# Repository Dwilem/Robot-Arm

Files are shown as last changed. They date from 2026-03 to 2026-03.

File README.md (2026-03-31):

# Robot-Arm
# Description
Pretty basic robotic 5 axis robotic arm, containing these axis: base, shoulder, elboew, wristx, wristy. To recreate this project, you can 3d print it, assemble it and upload provided firmware.

# Why
My main goal building such device, was deepen my knowledge of robotics, improve my electrical and mechanical fields. As well it is pretty cool project in general.

# Notes 
- Altough my main idea was to add camera to it, it turned out to be way more complicated, so I dumped that idea.
- If you want smoother movement of arm, I don't recommend buying cheapest knock-off motors and instead investing a bit more money into this. As I described in my journal, motors I bought were falsly advertised, so robot was failing :/.
- I recommend using different power supplys for Esp and motors, due to stability issues.
- Blue parts in Model\Asembly.step showcase where perf boards and esp is mounted.
- Perf boards serve as place for pin heads to be soldered on, so entire assmebly would be easier to take appart and maintain, without constant resoldering.

# Gallery
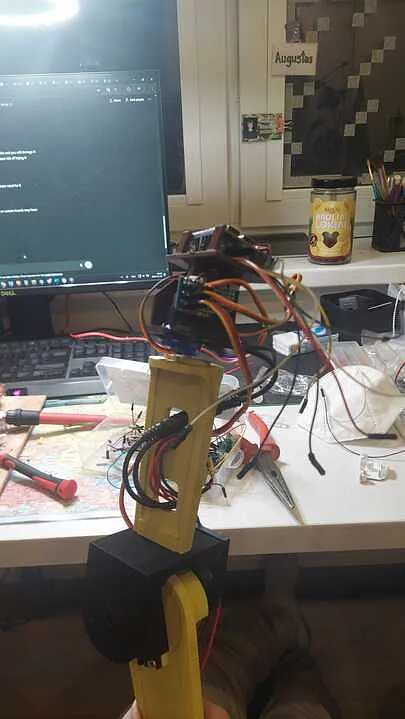
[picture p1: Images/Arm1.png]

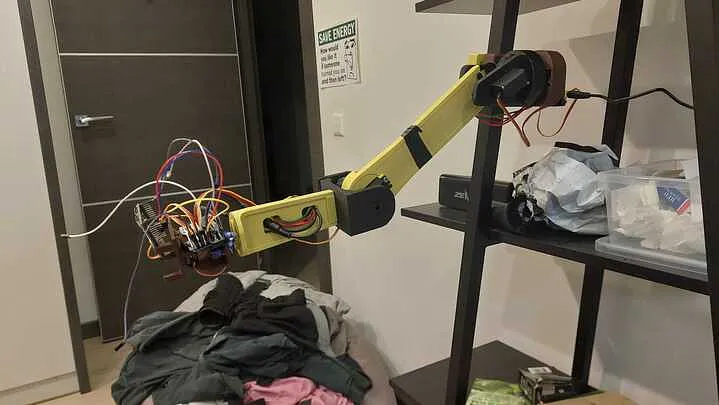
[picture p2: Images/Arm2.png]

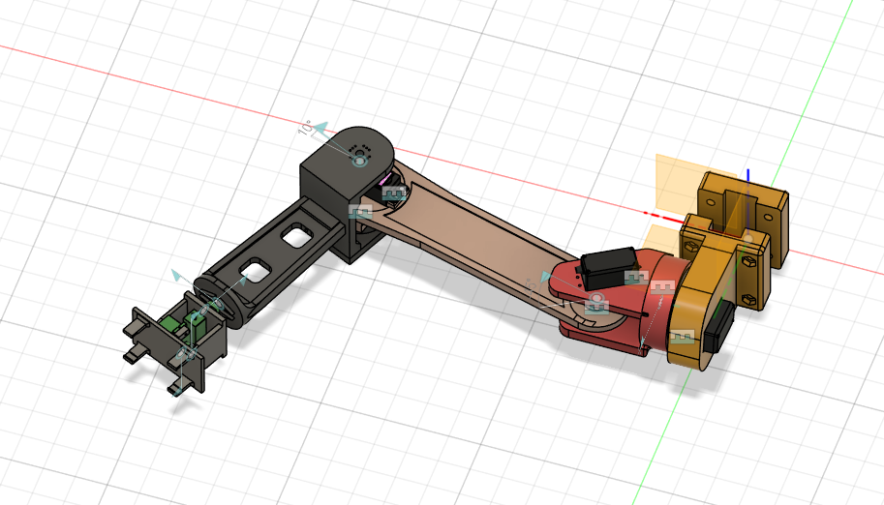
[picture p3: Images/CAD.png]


# Wiring
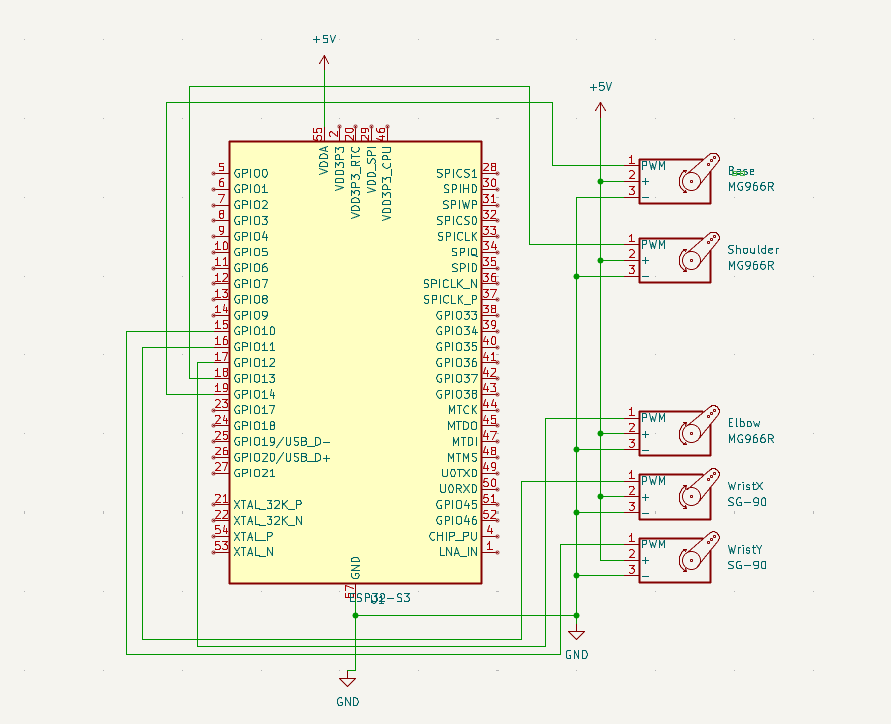
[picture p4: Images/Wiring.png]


# BOM
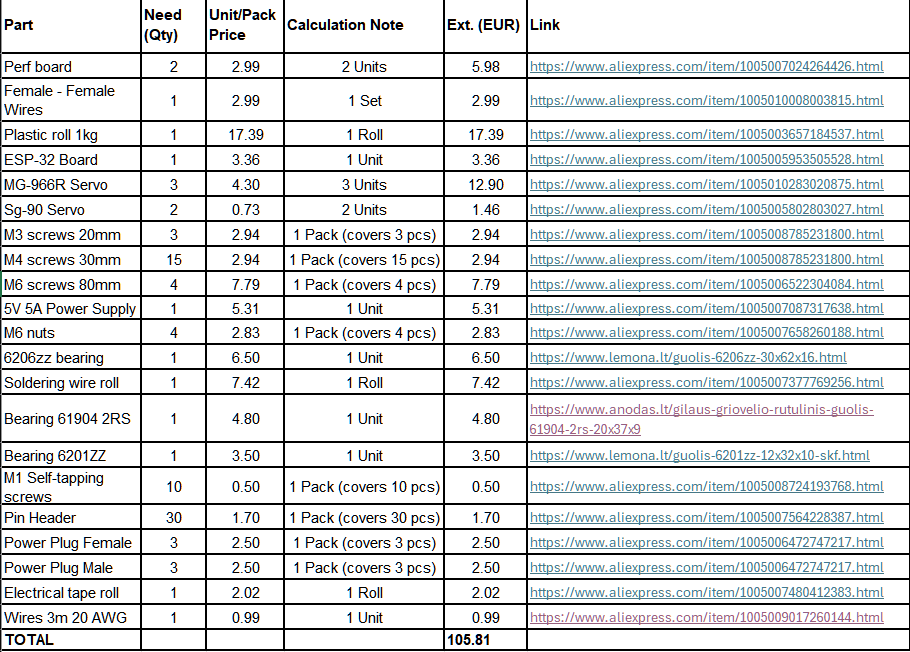
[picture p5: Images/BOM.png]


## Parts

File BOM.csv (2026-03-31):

Part | Need (Qty) | Unit/Pack Price | Calculation Note | Ext. (EUR) | Link
Perf board | 2 | 2.99 | 2 Units | 5.98 | https://www.aliexpress.com/item/1005007024264426.html
Female - Female Wires | 1 | 2.99 | 1 Set | 2.99 | https://www.aliexpress.com/item/1005010008003815.html
Plastic roll 1kg | 1 | 17.39 | 1 Roll | 17.39 | https://www.aliexpress.com/item/1005003657184537.html
ESP-32 Board | 1 | 3.36 | 1 Unit | 3.36 | https://www.aliexpress.com/item/1005005953505528.html
MG-966R Servo | 3 | 4.30 | 3 Units | 12.90 | https://www.aliexpress.com/item/1005010283020875.html
Sg-90 Servo | 2 | 0.73 | 2 Units | 1.46 | https://www.aliexpress.com/item/1005005802803027.html
M3 screws 20mm | 3 | 2.94 | 1 Pack (covers 3 pcs) | 2.94 | https://www.aliexpress.com/item/1005008785231800.html
M4 screws 30mm | 15 | 2.94 | 1 Pack (covers 15 pcs) | 2.94 | https://www.aliexpress.com/item/1005008785231800.html
M6 screws 80mm | 4 | 7.79 | 1 Pack (covers 4 pcs) | 7.79 | https://www.aliexpress.com/item/1005006522304084.html
5V 5A Power Supply | 1 | 5.31 | 1 Unit | 5.31 | https://www.aliexpress.com/item/1005007087317638.html
M6 nuts | 4 | 2.83 | 1 Pack (covers 4 pcs) | 2.83 | https://www.aliexpress.com/item/1005007658260188.html
6206zz bearing | 1 | 6.50 | 1 Unit | 6.50 | https://www.lemona.lt/guolis-6206zz-30x62x16.html
Soldering wire roll | 1 | 7.42 | 1 Roll | 7.42 | https://www.aliexpress.com/item/1005007377769256.html
Bearing 61904 2RS | 1 | 4.80 | 1 Unit | 4.80 | https://www.anodas.lt/gilaus-griovelio-rutulinis-guolis-61904-2rs-20x37x9
Bearing 6201ZZ | 1 | 3.50 | 1 Unit | 3.50 | https://www.lemona.lt/guolis-6201zz-12x32x10-skf.html
M1 Self-tapping screws | 10 | 0.50 | 1 Pack (covers 10 pcs) | 0.50 | https://www.aliexpress.com/item/1005008724193768.html
Pin Header | 30 | 1.70 | 1 Pack (covers 30 pcs) | 1.70 | https://www.aliexpress.com/item/1005007564228387.html
Power Plug Female | 3 | 2.50 | 1 Pack (covers 3 pcs) | 2.50 | https://www.aliexpress.com/item/1005006472747217.html
Power Plug Male | 3 | 2.50 | 1 Pack (covers 3 pcs) | 2.50 | https://www.aliexpress.com/item/1005006472747217.html
Electrical tape roll | 1 | 2.02 | 1 Roll | 2.02 | https://www.aliexpress.com/item/1005007480412383.html
Wires 3m 20 AWG | 1 | 0.99 | 1 Unit | 0.99 | https://www.aliexpress.com/item/1005009017260144.html
TOTAL |  |  |  | 105.81

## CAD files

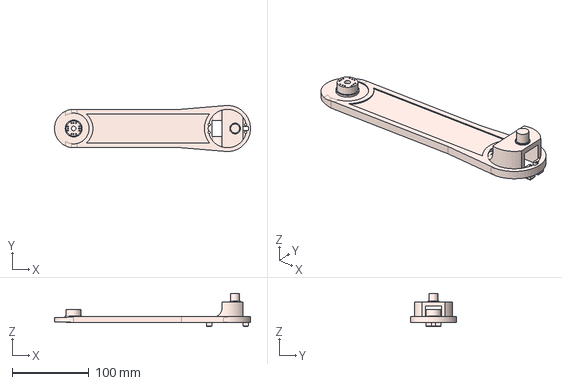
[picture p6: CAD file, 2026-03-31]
Model/Arm1/Arm1.step
255.0 x 60.0 x 43.0 mm

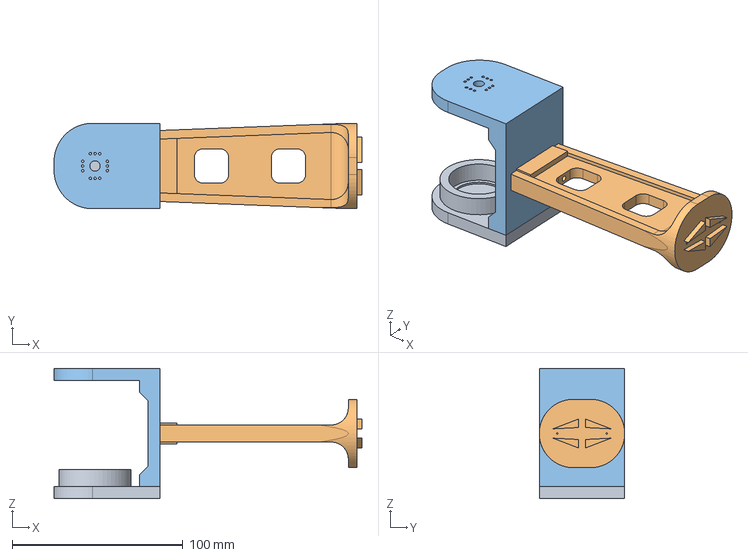
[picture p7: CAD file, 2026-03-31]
Model/Arm2/Arm2.step
180.1 x 50.0 x 76.2 mm

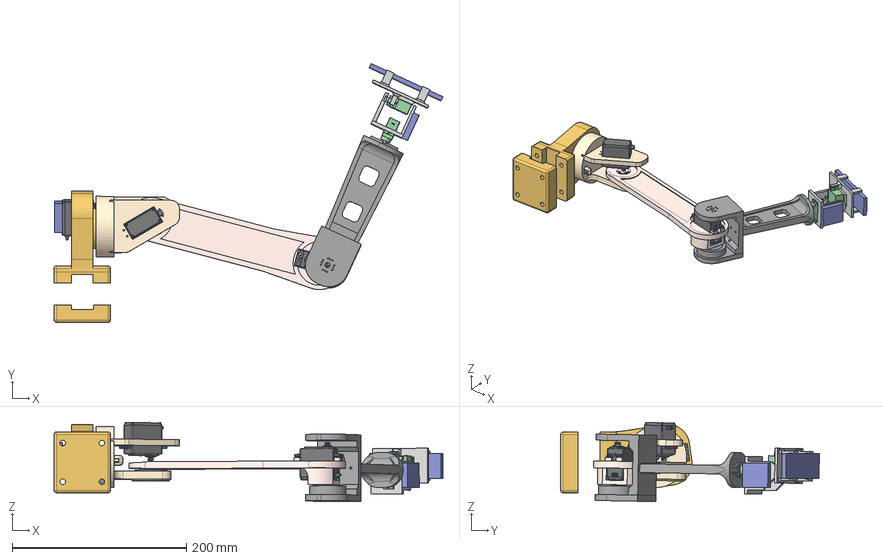
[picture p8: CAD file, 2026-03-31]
Model/Asembly.step
446.4 x 297.0 x 90.9 mm
Servo+MG996R x 3
Base
guolis-6206zz-30x62x16
Shoulder
Arm
servo x 2
splined-drive x 2
Wrist
Wrist2
Guolis 37-20-9
Guolis 32-20-10

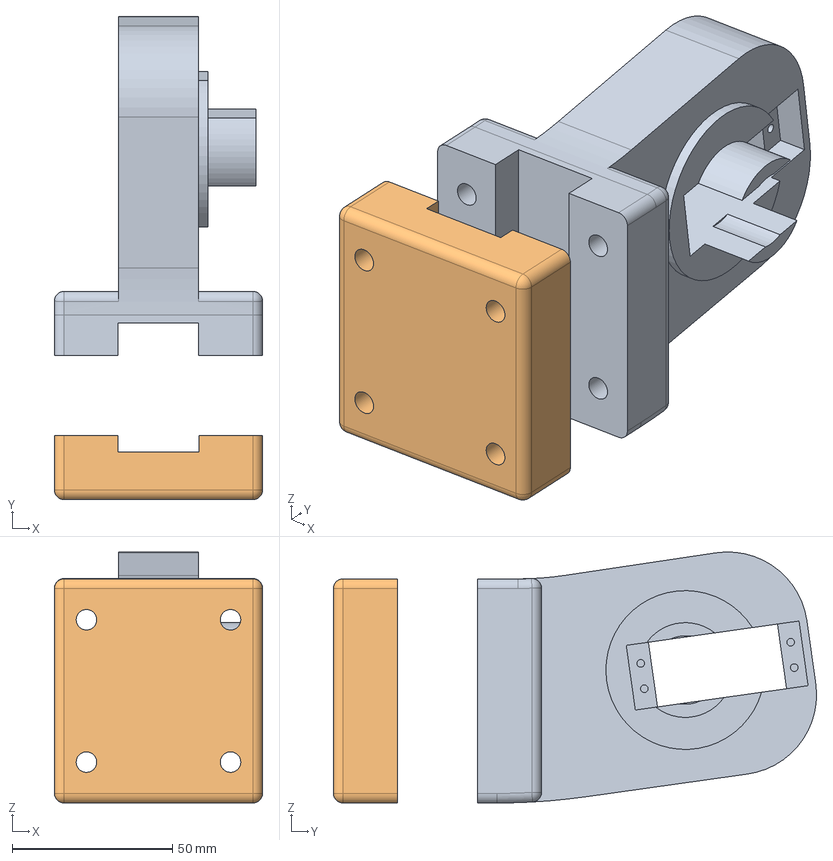
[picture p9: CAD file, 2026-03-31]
Model/Base/Base.step
65.0 x 150.9 x 78.4 mm

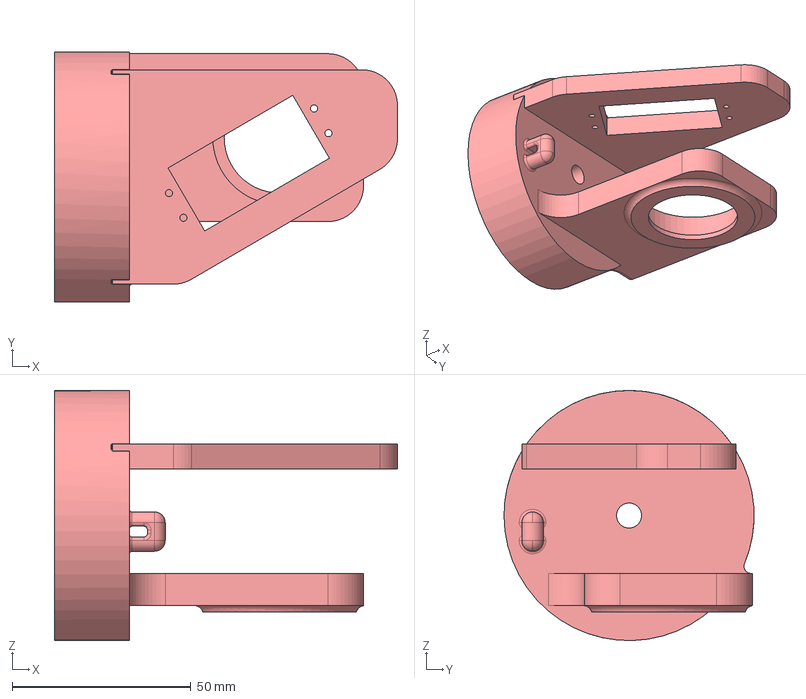
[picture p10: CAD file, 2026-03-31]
Model/Shoulder/Shoulder.step
96.0 x 70.0 x 70.0 mm

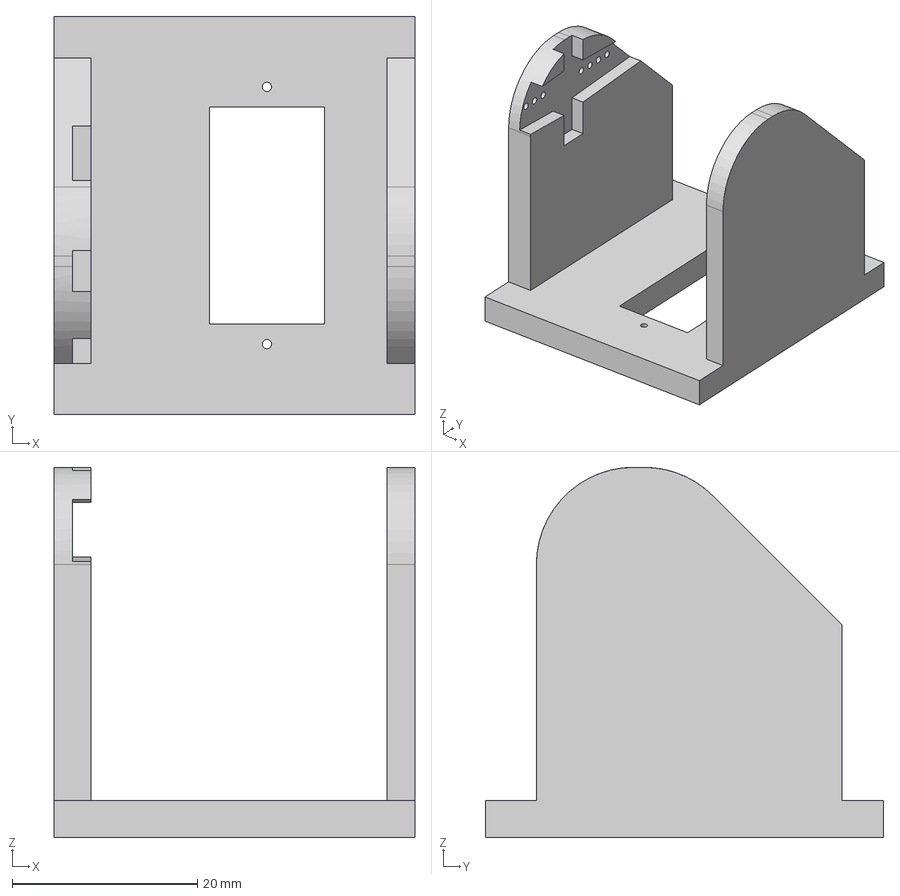
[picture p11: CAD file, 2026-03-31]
Model/Wrist1/Wrist1.step
39.0 x 43.0 x 40.0 mm

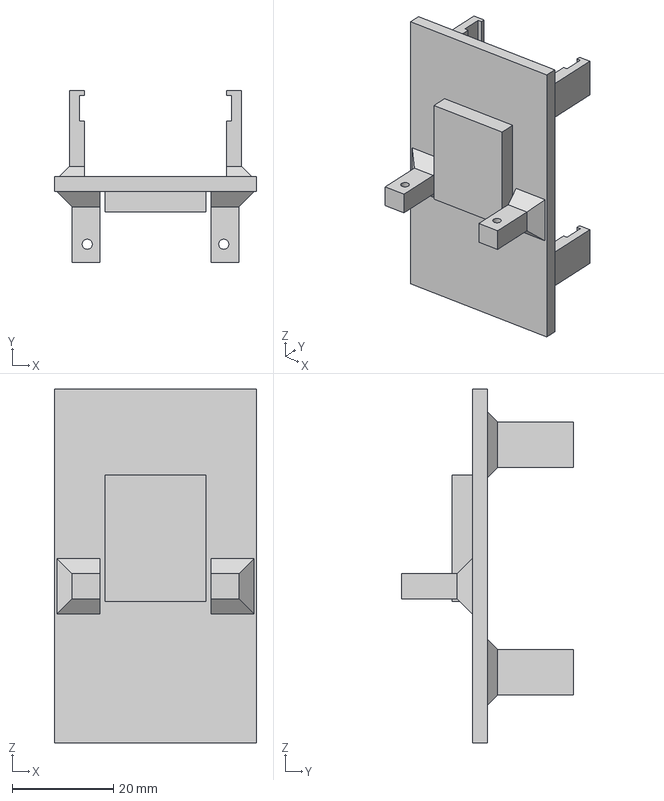
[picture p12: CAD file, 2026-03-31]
Model/Wrist2/Wrist2.step
40.0 x 34.0 x 70.0 mm

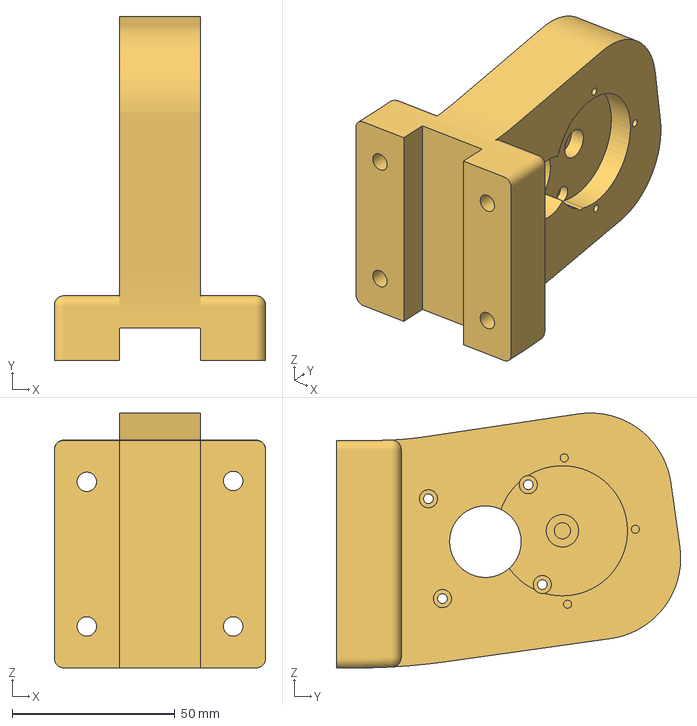
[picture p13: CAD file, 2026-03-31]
Printing/Body1.3mf
65.0 x 105.9 x 78.4 mm

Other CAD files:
Model/Arm1/Arm1.f3d
Model/Arm2/Arm2.f3d
Model/Asembly.f3z
Model/Base/Base.f3d
Model/Shoulder/Shoulder.f3d
Model/Wrist1/Wrist1.f3d
Model/Wrist2/Wrist2.f3d

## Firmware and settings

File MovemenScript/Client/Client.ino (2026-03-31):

#include <WiFi.h>
#include <WebSocketsClient.h>
#include <ArduinoJson.h>
#include <ESP32Servo.h>

// Wi-Fi
const char* ssid     = "***"; // CHANGE HERE
const char* password = "***"; // CHANGE HERE


// Server
const char* serverIP = "192.168.0.101";
const int serverPort = 8765;

// Servos
Servo Base, Shoulder, Elbow, WristX, WristY;

// Target angles
int targetBase = 90;
int targetShoulder = 90;
int targetElbow = 90;
int targetWristX = 90;
int targetWristY = 90;

// Speed (degrees per update)
int moveSpeed = 2;

WebSocketsClient webSocket;

// Smooth move function
int moveTowards(int current, int target, int step) {
  if (current < target) return min(current + step, target);
  if (current > target) return max(current - step, target);
  return current;
}

void webSocketEvent(WStype_t type, uint8_t * payload, size_t length) {
    switch(type) {
    case WStype_DISCONNECTED:
      Serial.println("[WebSocket] Disconnected");
      break;
    case WStype_CONNECTED:
      Serial.println("[WebSocket] Connected to server");
      break;
    case WStype_TEXT:
    {
      Serial.print("[WebSocket] Received: ");
      Serial.println((char*)payload);
      StaticJsonDocument<200> doc;
      if (deserializeJson(doc, payload) == DeserializationError::Ok) {
        targetBase = doc["Base"];
        targetShoulder = doc["Shoulder"];
        targetElbow = doc["Elbow"];
        targetWristX = doc["WristX"];
        targetWristY = doc["WristY"];
        moveSpeed = doc["Speed"];
      
      }
    }
  }
}

void setup() {
  Serial.begin(115200);

  WiFi.begin(ssid, password);
  while (WiFi.status() != WL_CONNECTED) {
    delay(300);
    Serial.print(".");
  }
  Serial.println("\nWiFi connected");

  // Attach servos to pins
  Base.attach(14);
  Shoulder.attach(13);
  Elbow.attach(12);
  WristX.attach(11);
  WristY.attach(10);

  // Initial positions
  Base.write(90);
  Shoulder.write(90);
  Elbow.write(90);
  WristX.write(90);
  WristY.write(90);

  webSocket.begin(serverIP, serverPort, "/");
  webSocket.onEvent(webSocketEvent);
  webSocket.setReconnectInterval(2000);
}

void loop() {
  webSocket.loop();

  // Gradually move servos toward targets
  Base.write(moveTowards(Base.read(), targetBase, moveSpeed));
  Shoulder.write(moveTowards(Shoulder.read(), targetShoulder, moveSpeed));
  Elbow.write(moveTowards(Elbow.read(), targetElbow, moveSpeed));
  WristX.write(moveTowards(WristX.read(), targetWristX, moveSpeed));
  WristY.write(moveTowards(WristY.read(), targetWristY, moveSpeed));

  delay(20); // ~50 updates per second
}

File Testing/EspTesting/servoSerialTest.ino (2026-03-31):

#include <ESP32Servo.h>

Servo myServo;

char buffer[8];
uint8_t bufIndex = 0;

void setup() {
  Serial.begin(115200);
  delay(2000);
  Serial.println("Enter angle 0‑180:");

  myServo.setPeriodHertz(50);    // Standard servo
  myServo.attach(8);             // Safe pin (not GPIO0)
}

void loop() {
  while (Serial.available()) {
    char c = Serial.read();

    if (c == '\n' || c == '\r') {
      buffer[bufIndex] = '\0';
      int angle = atoi(buffer);

      if (angle >= 0 && angle <= 180) {
        myServo.write(angle);
        Serial.print("Moved to: ");
        Serial.println(angle);
      } else {
        Serial.println("Invalid angle!");
      }

      bufIndex = 0;
    }
    else if (isDigit(c) && bufIndex < sizeof(buffer) - 1) {
      buffer[bufIndex++] = c;
    }
  }
}
